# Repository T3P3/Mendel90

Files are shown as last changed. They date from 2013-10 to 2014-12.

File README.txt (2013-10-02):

Mendel90 Lasercut
-----------------
The Think3dPrint3d variation of the Mendel90. Original Mendel90 source available here:
https://github.com/nophead/Mendel90

For the initial announcement of this design see my blog post here:
http://blog.think3dprint3d.com/2013/09/mendel90-laser-cut-ready-to-print.html

IMPORTANT NOTE:
The make_machine.py script will not work properly with this branch of the Mendel90,
the individual scad files will need to be compiled if you change variables. Also note that
the changes are not fully parametric so check the output before printing/lasercutting

======================================================================
Original text of Nophead's readme follows:
======================================================================

Limitations
-----------
Currently only supports mendel and sturdy machine variants, the huxley version needs more work.

Use
---
Add the directory of the OpenScad executable to your search path. For Windows OpenSCAD-2012.02 or later is required. For Linux it will need to be openscad-2011.12 or later.
To get PDF versions of the sheet drawings add InkScape to your search path.

To make all the files for a machine run
    make_machine.py machine_name

To make just the bom, sheets or stls run bom.py, sheets.py or stls.py machine_name.

machine_name can be mendel or sturdy. To make your own variant copy scad\conf\mendel_config.scad or scad\conf\sturdy_config.scad to yourname_config.scad.  Then run make_machine yourname.

To view the model of the whole machine, open scad\main.scad. It will take several minutes to render (about about 8 minutes on my computer) but after that you can pan and zoom it at reasonable speed and changes takes less time to render.  (Note: main.scad will only render correctly if conf\machine.scad exists, which is created by the make_machine.py script.)

To view a sub-assembly, open the individual scad files. Set the exploded flag in config.scad to make exploded views.

To get blender renders of all the parts put blender in your search path and run render.py machine_name.

Credits
-------
Fan model based on http://www.thingiverse.com/thing:8063 by MiseryBot, CC license.

Sanguinololu model http://www.thingiverse.com/thing:18606 by ax_the_b, CC license.

Spring taken from openscad example 20

x-end.scad and wade.scad use some elements of the Prusa ones by Josef Prusa, GPL license.

z_couplings originally based on http://www.thingiverse.com/thing:7153 by Griffin_Nicoll, GPL license.

Bearing holders originally based on http://www.thingiverse.com/thing:7755 by Jolijar, CC license.

InkCL.py based on code from http://kaioa.com/node/42

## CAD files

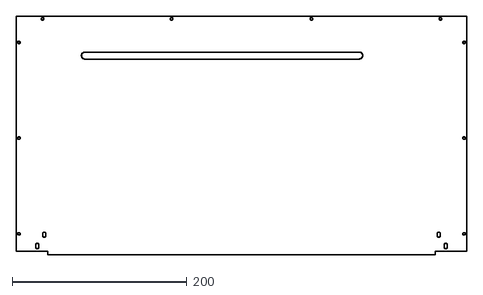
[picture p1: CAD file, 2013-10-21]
lasercut/sheets/T3P3_LC_M90_Acrylic_v1.0_top.dxf
515.5 x 273.0

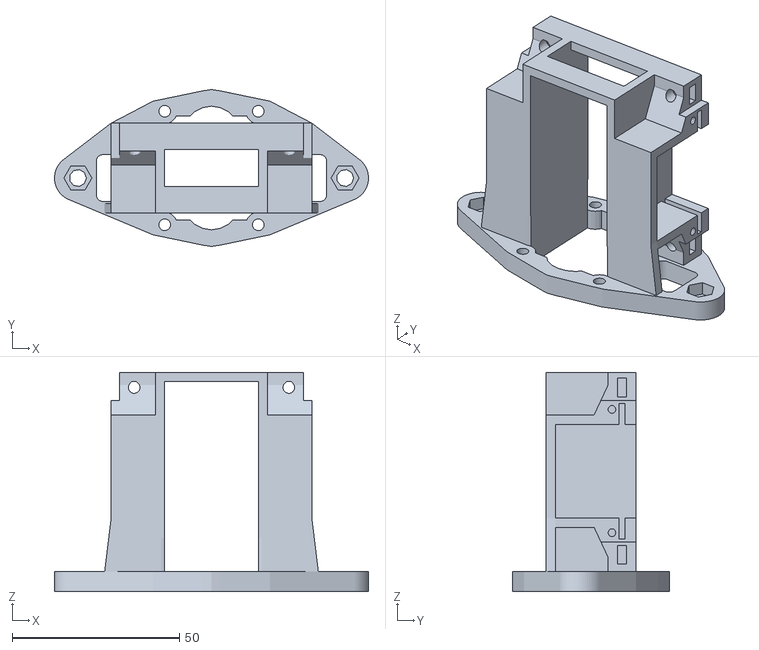
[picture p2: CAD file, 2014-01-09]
lasercut/stls/D_bracket_k_v0.2.stl
94.0 x 47.0 x 65.6

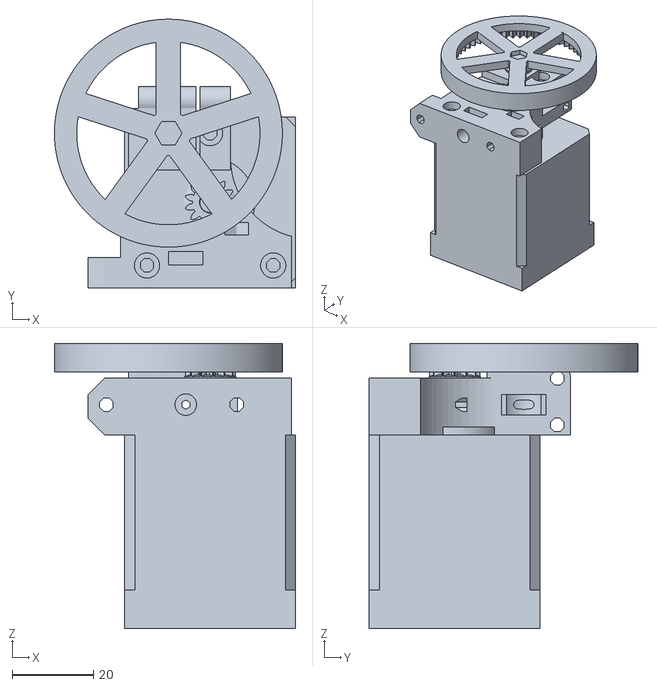
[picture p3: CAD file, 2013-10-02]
scad/rrp_extruder/extruder-drive.stl
59.2 x 66.0 x 70.0

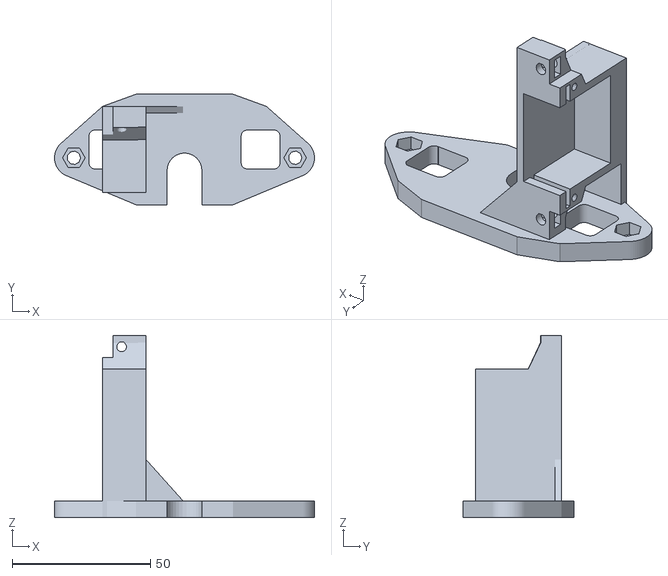
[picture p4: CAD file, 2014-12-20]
V2_upgrades/D_bracket_g_v0.2.stl
94.0 x 40.0 x 65.8

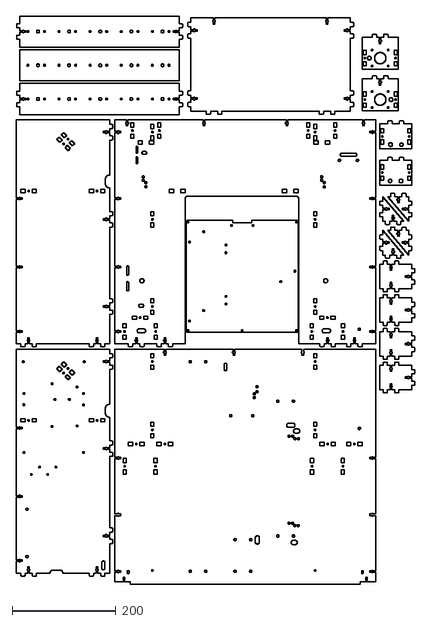
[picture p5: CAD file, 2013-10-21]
lasercut/sheets/T3P3_LC_M90_v1.0.dxf
768.5 x 1095.0

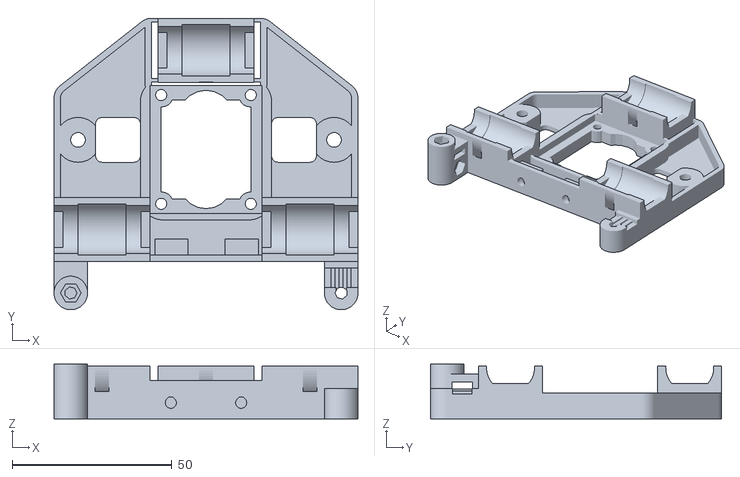
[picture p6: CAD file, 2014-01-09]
lasercut/stls/x-carriage_K_v0.2.stl
95.0 x 91.1 x 17.1

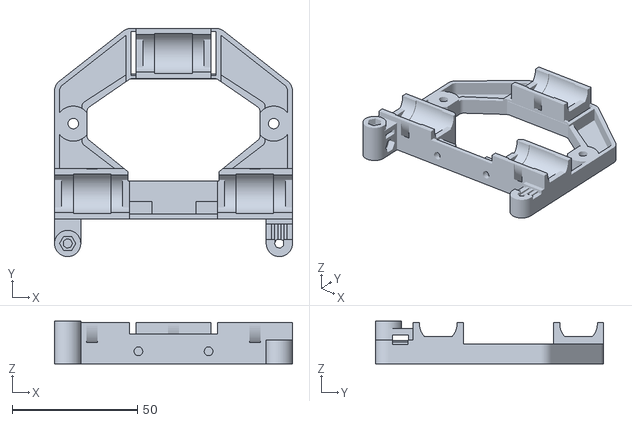
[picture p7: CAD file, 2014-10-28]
V2_upgrades/x-carriage - gv0.3.stl
95.0 x 91.1 x 17.1

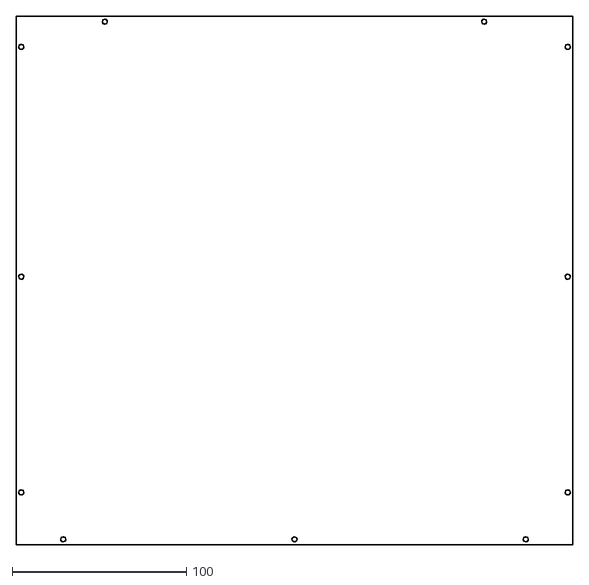
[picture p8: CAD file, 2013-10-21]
lasercut/sheets/T3P3_LC_M90_Acrylic_v1.0_back.dxf
319.9 x 303.6

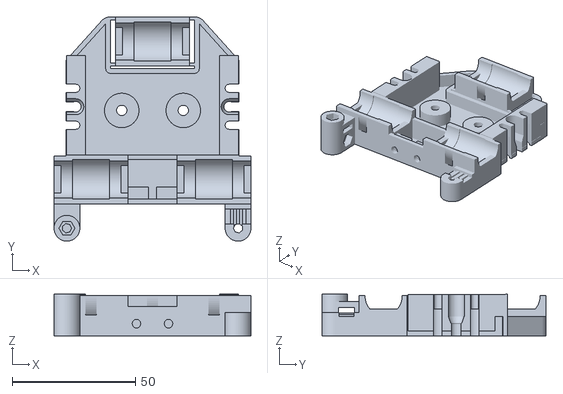
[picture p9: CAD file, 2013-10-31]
lasercut/stls/x-carriage_RRPEv0.3.stl
80.0 x 91.1 x 17.0

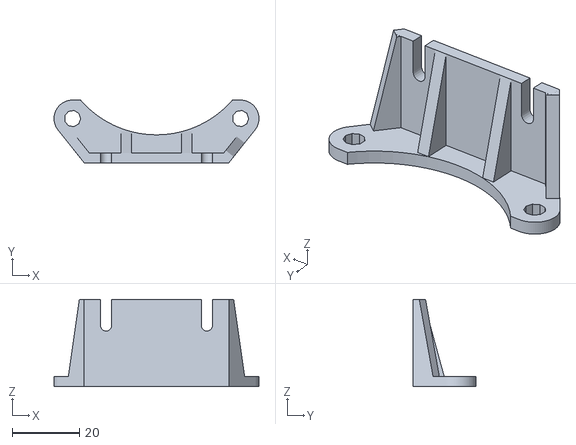
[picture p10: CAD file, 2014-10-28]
V2_upgrades/x_carriage_fan_bracket_e3dv6.stl
61.0 x 18.7 x 26.0

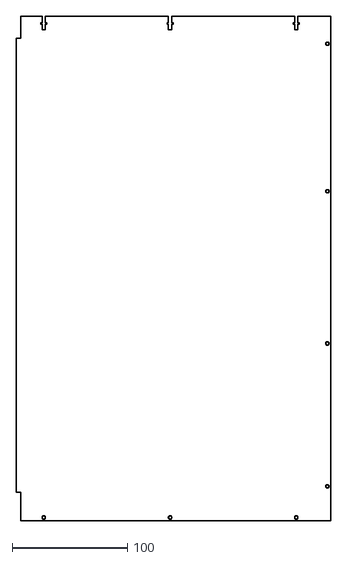
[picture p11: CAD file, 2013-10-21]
lasercut/sheets/T3P3_LC_M90_Acrylic_v1.0_side.dxf
273.0 x 438.0

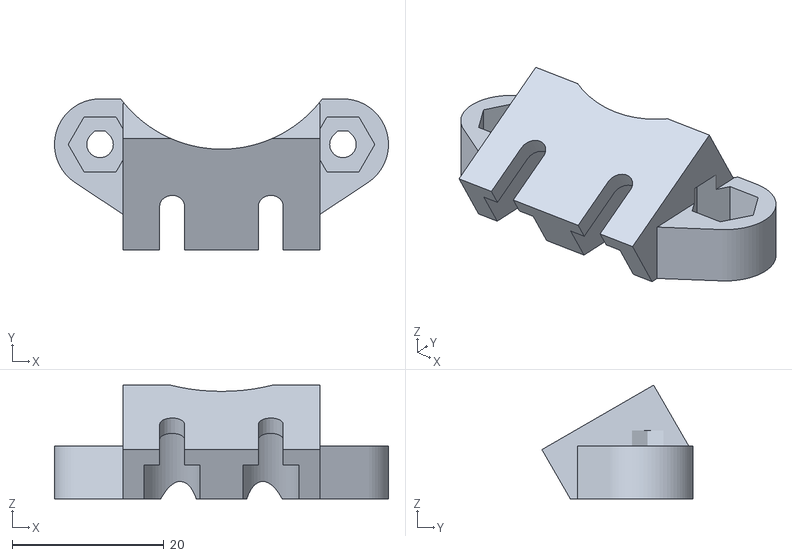
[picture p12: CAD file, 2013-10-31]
lasercut/stls/simple40mmfanbracket_RRPEv0.3.stl
44.0 x 19.9 x 15.0

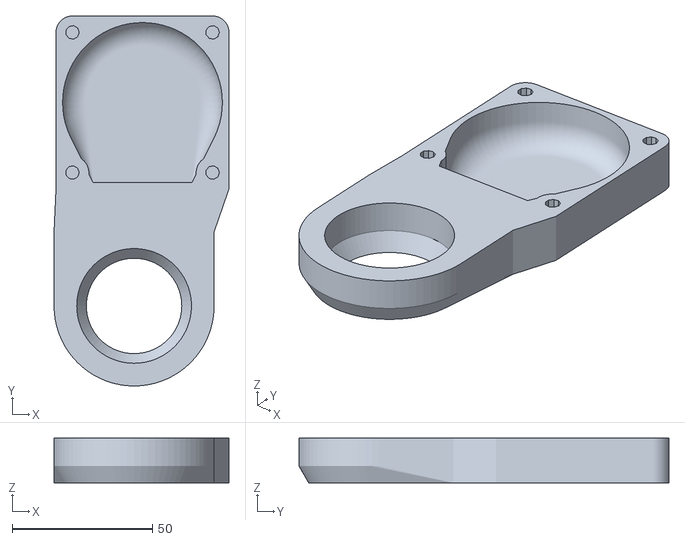
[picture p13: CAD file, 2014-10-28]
V2_upgrades/x_carriage_fan_duct_e3dv6_v2.stl
62.4 x 132.0 x 16.0

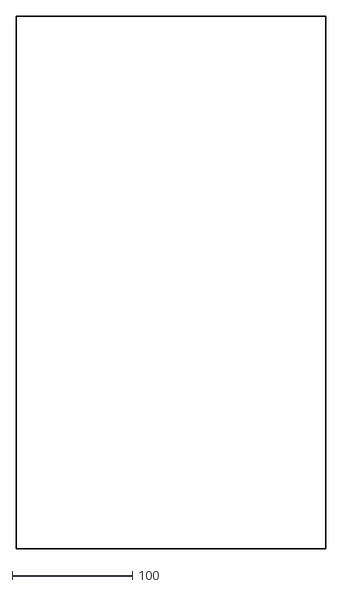
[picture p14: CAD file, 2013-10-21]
lasercut/sheets/T3P3_LC_M90_Acrylic_v1.0_door.dxf
257.8 x 444.0

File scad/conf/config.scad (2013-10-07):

//
// Mendel90
//
// GNU GPL v2
// nop.head@gmail.com
// hydraraptor.blogspot.com
//
// Configuration file
//
bom = $bom == undef ? 0: $bom;                 // 0 no bom, 1 assemblies and stls, 2 vitamins as well
exploded = $exploded == undef ? 0 : $exploded; // 1 for exploded view
//exploded =1;
show_jigs = true;               // show printed jigs required to build the machine
show_support = true;            // show support structures, must be set when generating STLs

// Real-world colors for various parts & vitamins
use_realistic_colors = false;    // true for "real" colors, false for "distinct" colors (useful during design and for build instructions)
printed_plastic_color = "blue";
cable_strip_real_color = "fuchsia";
belt_real_color = "yellow";
bulldog_real_color ="black";

eta = 0.01;                     // small fudge factor to stop CSG barfing on coincident faces.
$fa = 5;
$fs = 0.5;

//
// Hole sizes
//
No2_pilot_radius = 1.7 / 2;       // self tapper into ABS
No4_pilot_radius = 2.0 / 2;       // wood screw into soft wood
No6_pilot_radius = 2.0 / 2;       // wood screw into soft wood

No2_clearance_radius = 2.5 / 2;
No4_clearance_radius = 3.5 / 2;
No6_clearance_radius = 4.0 / 2;

M2p5_tap_radius = 2.05 / 2;
M2p5_clearance_radius= 2.8 / 2;   // M2.5
M2p5_nut_trap_depth = 2.5;

M3_tap_radius = 2.5 / 2;
M3_clearance_radius = 3.3 / 2;
M3_nut_radius = 6.5 / 2;
M3_nut_trap_depth = 3;

M4_tap_radius = 3.3 / 2;
M4_clearance_radius = 2.2;
M4_nut_radius = 8.2 / 2;
M4_nut_trap_depth = 4;

M5_tap_radius = 4.2 / 2;
M5_clearance_radius = 5.3 / 2;
M5_nut_radius = 9.2 / 2;
M5_nut_depth = 4;

M6_tap_radius = 5 / 2;
M6_clearance_radius = 6.4 / 2;
M6_nut_radius = 11.6 / 2;
M6_nut_depth = 5;

M8_tap_radius = 6.75 / 2;
M8_clearance_radius = 8.4 / 2;
M8_nut_radius = 15.4 / 2;
M8_nut_depth = 6.5;

cnc_tool_dia = 0.5;
layer_height = 0.4;
filament_width = layer_height * 1.5;
min_wall = 2 * filament_width + eta;
part_base_thickness = 5;;           // The thickness of things screwed to the frame

pcb_thickness = 1.6;
feed_tube_rad = 5 / 2;              // Filament feed tube
feed_tube_tape_rad = 6.2 / 2;
feed_tube_tape = 12;
nozzle_length = 54;                 // how far nozzle is below top of carriage


include <colors.scad>
include <utils.scad>
include <vitamins.scad>

endstop_wires    = [2, 1.4, "A"];   // 7 strands of 0.2
motor_wires      = [4, 1.4, "B"];
bed_wires        = [2, 2.8, "C"];   // 13A mains cable
fan_motor_wires  = [6, 1.4, "D"];   // fan and motor wires along top of gantry
two_motor_wires  = [8, 1.4,,"E"];   // Y and Z motors
thermistor_wires = endstop_wires;

endstop_wires_hole_radius = wire_hole_radius(endstop_wires);
motor_wires_hole_radius = wire_hole_radius(motor_wires);
two_motor_wires_hole_radius = wire_hole_radius(two_motor_wires);
fan_motor_wires_hole_radius = wire_hole_radius(fan_motor_wires);
bed_wires_hole_radius = wire_hole_radius(bed_wires);
thermistor_wires_hole_radius = wire_hole_radius(thermistor_wires);

cnc_sheets = false;                 // If sheets are cut by CNC we can use slots, etc instead of just round holes
base_nuts = true;                  // Need something under the base if using nuts
pulley_type = T5x8_plastic_pulley;
clip_handles = true;
include_fan = false;
part_fan = fan60x15;
include <machine.scad>              // this file is generated from the command line parameter to include one of the machine configs

screw_clearance_radius = screw_clearance_radius(cap_screw);
nut = screw_nut(cap_screw);
nut_radius = nut_radius(nut);
nut_trap_depth = nut_trap_depth(nut);
washer = screw_washer(cap_screw);

bearing_clamp_tab = cnc_sheets ? (nut_radius(nut) + 3 * filament_width) * 2 : washer_diameter(washer) + 2;   // how much the lugs stick out and their width
bearing_clamp_tab_height = 4;           // thickness of the lugs

hole_edge_clearance = 5;                // how close a hole can be to the edge of a sheet
base_clearance = cnc_sheets ? 4 : 4;    // how close we get to the edge of the base
axis_end_clearance = cnc_sheets ? 4 : 4;// how close we get to the end of an axis
limit_switch_offset = 1;                // the over travel to reach the limit switch
X_carriage_clearance = 2;               // how close the X carriage is to the XZ plane
                                        // how close the Y carriage is to the window in the XZ plane
Y_carriage_clearance = 2 + bulldog_handle_length(small_bulldog) - (Y_carriage_width - bed_width) / 2;
Z_clearance = 10;                       // How close the top of the object gets to the gantry
belt_clearance = 0.2;                   // clearance of belt clamp slots

X_bar_dia = X_bearings[2];      // rod sizes to match the bearings
Y_bar_dia = Y_bearings[2];
Z_bar_dia = Z_bearings[2];

Y_idler_bearing = BB624;
X_idler_bearing = BB624;

extruder_ways = 4 + 6 + 2 + 1 + 1;      // motor + heater(x3) + thermistor + probe + fan = 14
x_end_ways = extruder_ways + 4 + 2;     // motor plus limit switch = 20
bed_ways = 24 + 2;                      // twelve each way for the current plus a thermistor

module wire_hole_or_slot(r) {
    if(cnc_sheets)
        rotate([0, 0, 90])
            slot(r = r, h = 100, l = 2 * r);
    else
        translate([0, r + hole_edge_clearance, 0])
            wire_hole(r);
}

function z_bar_offset() = round(NEMA_width(Z_motor)) / 2;

base_screw = sheet_is_soft(base) ? frame_soft_screw : (base_nuts ? frame_thin_screw : frame_thick_screw);
base_nut = base_nuts ? screw_nut(base_screw) : false;
base_nut_traps = base_nuts && cnc_sheets;
base_washer = screw_washer(base_screw);
base_screw_length = base_nuts ? screw_longer_than(
                                    sheet_thickness(base)
                                    + part_base_thickness +
                                    (cnc_sheets ? 1 : 2) * washer_thickness(base_washer)
                                    + nut_thickness(base_nut, true)
                                  )
                              : screw_shorter_than(
                                    sheet_thickness(base)
                                    + part_base_thickness
                                    + 2 * washer_thickness(base_washer)
                                 );


frame_screw = sheet_is_soft(frame) ? frame_soft_screw : (frame_nuts ? frame_thin_screw : frame_thick_screw);
frame_nut = frame_nuts ? screw_nut(frame_screw) : false;
frame_nut_traps = frame_nuts && cnc_sheets;
frame_washer = screw_washer(frame_screw);
frame_screw_length = frame_nuts ? screw_longer_than(
                                      sheet_thickness(frame)
                                      + part_base_thickness +
                                      (cnc_sheets ? 1 : 2) * washer_thickness(frame_washer)
                                      + nut_thickness(frame_nut, true)
                                  )

                                : screw_shorter_than(
                                      sheet_thickness(frame)
                                      + part_base_thickness
                                      + 2 * washer_thickness(frame_washer)
                                  );

echo("base screw length", base_screw_length);
echo("frame screw length",frame_screw_length);



module frame_screw(thickness) {
    if(frame_nuts && cnc_sheets) {
        nut(frame_nut, true);
        translate([0, 0, -sheet_thickness(frame) - thickness])
            rotate([180, 0, 0])
                screw_and_washer(frame_screw, frame_screw_length);
    }
    else {
        screw_and_washer(frame_screw, frame_screw_length, !frame_nuts);
        if(frame_nuts)
            translate([0, 0, -sheet_thickness(frame) - thickness])
                rotate([180, 0, 0])
                    nut_and_washer(frame_nut, true);
    }
}

module frame_screw_hole() {
    cylinder(r = frame_nuts ? screw_clearance_radius(frame_screw) : screw_pilot_hole(frame_screw), h = 100, center = true);
}



module base_screw(thickness) {
    if(base_nuts && cnc_sheets) {
        nut(base_nut, true);
        translate([0, 0, -sheet_thickness(base) - thickness])
            rotate([180, 0, 0])
                screw_and_washer(base_screw, base_screw_length);
    }
    else {
        screw_and_washer(base_screw, base_screw_length, !base_nuts);
        if(base_nuts)
            translate([0, 0, -sheet_thickness(base) - thickness])
                rotate([180, 0, 0])
                    nut_and_washer(base_nut, true);
    }
}

module base_screw_hole() {
    cylinder(r = base_nuts ? screw_clearance_radius(base_screw) : screw_pilot_hole(base_screw), h = 100, center = true);
}

bar_clamp_depth = 4 + washer_diameter(base_washer);           // how thick the bar clamps are
bar_clamp_tab = 3 + washer_diameter(base_washer);             // how much the lugs stick out
bar_clamp_band = 3;                                           // the thickness of the strap that clamps the bar.

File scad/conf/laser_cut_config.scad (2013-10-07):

//
// Mendel90
//
// GNU GPL v2
// nop.head@gmail.com
// hydraraptor.blogspot.com
//
// Configuration file
//

echo("LaserCut:");

Z_bearings = LM8UU;
Y_bearings = LM8UU;
X_bearings = LM8UU;

X_motor = NEMA17;
Y_motor = NEMA17;
Z_motor = NEMA17;

hot_end = JHeadMk5;

X_travel = 200;
Y_travel = 200;
Z_travel = 200;

bed_depth = 214;
bed_width = 214;
bed_pillars = M3x20_pillar;
bed_glass = glass2;
bed_thickness = pcb_thickness + sheet_thickness(bed_glass);    // PCB heater plus glass sheet
bed_holes = [209, 209];


base = MelamineMDF6;          
base_corners = 0;
base_nuts = true;

frame = MelamineMDF6;
frame_corners = 0;
frame_nuts = true;

case_fan = fan80x38;
psu = ALPINE500;
controller = RAMPS;
spool = spool_300x85;
bottom_limit_switch = false;
top_limit_switch = true;

single_piece_frame = true;
stays_from_window = false;
cnc_sheets = true;                 // If sheets are cut by CNC we can use slots, etc instead of just round holes
lc_sheets = true; //use the laser cut fixing method and additional slots for ease of assembly
lc_fixing_offset=24; //how far from an edge to put a LC fixing
lc_fixing_screw_type = M3_cap_screw;  
lc_fixing_screw_length = 16; //sheet_thickness(base)+10;

//additional dimensions for some sheets for LC M90
base_w_LC = 468.5+35;//base_width+10+25;
base_d_LC = 425+28;//base_depth+28;
height_LC = 390+12+30;//height+12+53;
stay_depth_LC=166+14;//stay_depth+14;
stay_height_LC=height_LC;


pulley_type = T2p5x16_metal_pulley;

Y_carriage = DiBond;

X_belt = T2p5x6;
Y_belt = T2p5x6;

motor_shaft = 5;
Z_screw_dia = 5;            // Studding for Z axis

Y_carriage_depth = bed_holes[1] + 7;
Y_carriage_width = bed_holes[0] + 7;

Z_nut_radius = M5_nut_radius;
Z_nut_depth = M5_nut_depth;
Z_nut = M5_nut;

//
// Default screw use where size doesn't matter
//
cap_screw = M3_cap_screw;
hex_screw = M3_hex_screw;
//
// Screw for the frame and base
//
frame_soft_screw = No6_screw;               // Used when sheet material is soft, e.g. wood
frame_thin_screw = M4_cap_screw;            // Used with nuts when sheets are thin
frame_thick_screw = M4_pan_screw;           // Used with tapped holes when sheets are thick and hard, e.g. plastic or metal
//
// Feature sizes
//
default_wall = 3;
thick_wall = 4;

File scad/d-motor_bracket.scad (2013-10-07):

//
// Mendel90
//
// GNU GPL v2
// nop.head@gmail.com
// hydraraptor.blogspot.com
//
// Bracket to mount 9 way D type to back of motor
//
include <conf/config.scad>
use <ribbon_clamp.scad>

connector = DCONN15;
pcb = true;
idc = true;

thickness = 2.4;
lid_thickness = 2.4;

wall = 2;
front_thickness = wall + No2_pilot_radius + washer_diameter(M2p5_washer) / 2 + 1;
slot_width = d_slot_length(connector);
slot_height = 11;
face_height = 13;
flange_clearance = 0.7;
flange_width = d_flange_length(connector) + 2 * flange_clearance;
flange_height = d_flange_width(connector) + flange_clearance;
flange_thickness = d_flange_thickness(connector) + flange_clearance;


overlap = 5;                            // how much it overlaps the side of the motor
//length = overlap + thickness + (pcb ? 14 : 20);
length = overlap + thickness + 20;
height = slot_height / 2 + face_height / 2 + thickness;
d_width = flange_width + 2 * wall;
nut_slot = nut_thickness(M3_nut) + 0.3;
lug_depth = nut_slot + 3 * wall;
lug_width = 2 * nut_flat_radius(M3_nut) + wall;
lug_height = thickness + slot_height / 2 + M3_nut_radius;
screw_x = length - wall - No2_pilot_radius;
screw_y = (d_width + slot_width) / 4;
pitch = d_width + 2 * nut_flat_radius(M3_nut);

cable_guide_width = 20;
cable_guide_thickness = 4;
cable_screw = M3_cap_screw;

shell_front = front_thickness;
shell_length = shell_front + 12 + ribbon_clamp_width(cable_screw);
shell_screw_x = shell_length - wall - No2_pilot_radius;

pcb_width = 24.13;
pcb_length = 33.02;
pcb_offset = 3 * 1.27;


nut_x = length + flange_thickness + wall -lug_depth + wall;

function d_motor_bracket_offset(motor) = NEMA_holes(motor)[0] + screw_head_radius(M3_cap_screw) + d_width / 2 + lug_width;

//
// Lid to retain connector and nuts
//
module d_motor_bracket_lid_stl(motor = NEMA17, nuts = true) {
    if(nuts)
        stl("d_motor_bracket_lid");
    else
        stl("d_shell_lid");

    lid_width = front_thickness + flange_thickness + wall;
    nut_cover_width = d_width + 2 * lug_width;
    nut_cover_height = height + lid_thickness - lug_height - flange_clearance;
    nut_cover_depth = lug_depth;

    difference() {
        union() {
            if(nuts) {
                translate([length - front_thickness + lid_width - nut_cover_depth / 2, 0, 0])
                    rounded_rectangle([nut_cover_depth, nut_cover_width, nut_cover_height], 2, center = false);
                for(side = [-1, 1])
                    translate([screw_x,  side * screw_y, 0])
                        cylinder(r = washer_diameter(M2p5_washer) / 2 + 2, h = lid_thickness);
            }
            else
                translate([length - front_thickness + lid_width / 2, 0, 0])
                    rounded_rectangle([lid_width, d_width, lid_thickness], 2, center = false);
        }

        if(nuts)
            translate([length - nut_cover_depth, -d_width / 2 - flange_clearance, lid_thickness - eta])
                cube([nut_cover_depth * 2, d_width + 2 * flange_clearance, 10]);

        for(side = [-1, 1])
            translate([screw_x,  side * screw_y, 0])
                rotate([0, 0, -side * 360 / 20])
                    poly_cylinder(r = No2_clearance_radius, h = 100, center = true);
    }
}

module d_shell_lid_stl() d_motor_bracket_lid_stl(motor = NEMA17, nuts = false);
//
// Attaches to the motor
//
module d_motor_bracket_stl(motor = NEMA17) {
    stl("d_motor_bracket");

    m_width = NEMA_width(motor) + 2 * thickness;
    offset = d_motor_bracket_offset(motor) + (m_width - d_width) / 2;
    mouth = pitch + 2 * M3_clearance_radius + layer_height / 2;

    difference() {
        union() {
            linear_extrude(height = thickness, convexity = 5)       // base
                polygon(points = [ [0,                        0],
                                   [overlap,                  0],
                                   [overlap,             offset],
                                   [length - eta,        offset],
                                   [length - eta,        offset + d_width],
                                   [overlap,             offset + d_width],
                                   [overlap,             m_width],
                                   [0,                   m_width],
                                 ]);

            translate([overlap , 0, eta])                               // motor wall
                cube([thickness, d_width + offset, height]);

            for(y = [0, m_width - thickness])                           // buttresses
                translate([overlap + eta, y, thickness - eta])
                    rotate([90, 0, 180])
                        right_triangle(width = overlap, height = height - thickness, h = thickness, center = false);


            difference() {
                union() {
                    // connector wall
                    translate([length - front_thickness, offset, eta])
                        cube([front_thickness + flange_thickness + wall, d_width, height]);

                    // nut lugs
                    translate([length + flange_thickness + wall - lug_depth / 2, offset + d_width / 2, eta])
                        rounded_rectangle([lug_depth, d_width + 2 * lug_width, lug_height], r = 2, center = false);

                    // d side walls
                    for(y = [0, d_width - thickness])
                        translate([overlap, y + offset, eta])
                            cube([length - overlap, thickness, height]);
                }

                translate([length, offset + (d_width - flange_width) / 2, thickness + slot_height / 2 - flange_height / 2])
                    cube([flange_thickness, flange_width, 20]);                         // slot for flange

                translate([10, d_width / 2 - slot_width / 2 + offset, thickness + eta * 2])  //slot for connector body
                    cube([30, slot_width, 20]);


                for(side = [-1, 1]) {
                    translate([nut_x + nut_slot / 2, d_width / 2 - side * pitch / 2 + offset, thickness + slot_height / 2]) //connector screws
                        rotate([90, 0, 90]) {
                            rotate([0,0,30])
                                nut_trap(1, M3_nut_radius, nut_slot / 2, true);

                            translate([0, 5, 0])
                                cube([nut_flat_radius(M3_nut) * 2, 10, nut_slot], center = true);

                            teardrop_plus(r = M3_clearance_radius, h = 100, center = true);
                        }

                    translate([screw_x, d_width / 2 - side * screw_y + offset, height + lid_thickness])         // lid screws holes
                        rotate([0,0,180])
                            poly_cylinder(r = No2_pilot_radius, h = 12 * 2, center = true);
                }

            }


        }
        for(y = NEMA_holes(motor))                                                          // motor screws
            for(z = NEMA_holes(motor))
                translate([overlap - 1, m_width / 2 + y, NEMA_width(motor) / 2 + thickness + z])
                    rotate([90,0,90])
                        teardrop_plus(r = M3_clearance_radius, h = thickness + 2, center = false);
    }
}
//
// Attaches connector to ribbon cable and plastic strip
//
function d_motor_connector_offset(motor) = [
    NEMA_width(motor) / 2 + thickness - cable_guide_thickness + ribbon_clamp_slot_depth(),
    -NEMA_length(motor) + overlap - length - d_mate_distance(connector) - shell_length + ribbon_clamp_width(cable_screw),
    d_motor_bracket_offset(motor)
];

module d_shell_stl() {
    stl("d_shell");

    mouth = pitch + 2 * screw_clearance_radius(cable_screw) + layer_height / 2;
    rad = ribbon_clamp_width(cable_screw) / 2;
    clamp_pitch = ribbon_clamp_pitch(extruder_ways, cable_screw);

    front = shell_front + flange_thickness + wall;
    union() {
        difference() {
            union() {
               // screw lugs
               translate([shell_length + flange_thickness + wall - front / 2, d_width / 2, eta])
                    rounded_rectangle([front, d_width + 2 * lug_width,
                                       thickness + slot_height / 2 + washer_diameter(M3_washer) / 2 + 1], r = 2, center = false);

               translate([shell_length + flange_thickness + wall - front / 2, d_width / 2, eta])        // connector wall
                    rounded_rectangle([front, d_width, height], r = 2, center = false);

               linear_extrude(height = cable_guide_thickness, convexity = 5)
                    hull() {
                        for(side = [-1,1])
                            translate([rad, d_width / 2 + side * clamp_pitch / 2])
                                circle(r = rad, center = true);

                        translate([shell_length - shell_front, 0])
                            square([1, d_width]);
                    }
            }
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

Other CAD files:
lasercut/stls/D_bracket_RRPEv0.3.stl
lasercut/stls/x_end_clamp.stl
lasercut/stls/x_carriage_fan_duct.stl
lasercut/stls/x_motor_ribbon_bracket.stl
scad/z-motor-bracket.scad
V2_upgrades/x-carriage - gv1.scad
lasercut/stls/ATX_PSU_brackets.stl
lasercut/stls/alu_channel_cap.stl
lasercut/stls/d-motor_bracket.stl
lasercut/stls/d_motor_bracket.stl
lasercut/stls/d_motor_bracket_lid.stl
lasercut/stls/d_shell.stl
lasercut/stls/d_shell_lid.stl
lasercut/stls/ribbon_clamp_14_33.stl
lasercut/stls/ribbon_clamp_14_33NB.stl
lasercut/stls/ribbon_clamp_20_33.stl
lasercut/stls/ribbon_clamp_20_44.stl
lasercut/stls/ribbon_clamp_20_44N.stl
lasercut/stls/ribbon_clamp_26_33.stl
lasercut/stls/ribbon_clamp_26_33N.stl
lasercut/stls/ribbon_clamp_26_44N.stl
lasercut/stls/ribbon_clamps.stl
lasercut/stls/wades_big_gear.stl
lasercut/stls/wades_block.stl
lasercut/stls/wades_gear_spacer.stl
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

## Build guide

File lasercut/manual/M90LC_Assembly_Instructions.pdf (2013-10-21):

www.think3dprint3d.com

# Mendel90 Laser Cut Kit Assembly Instructions

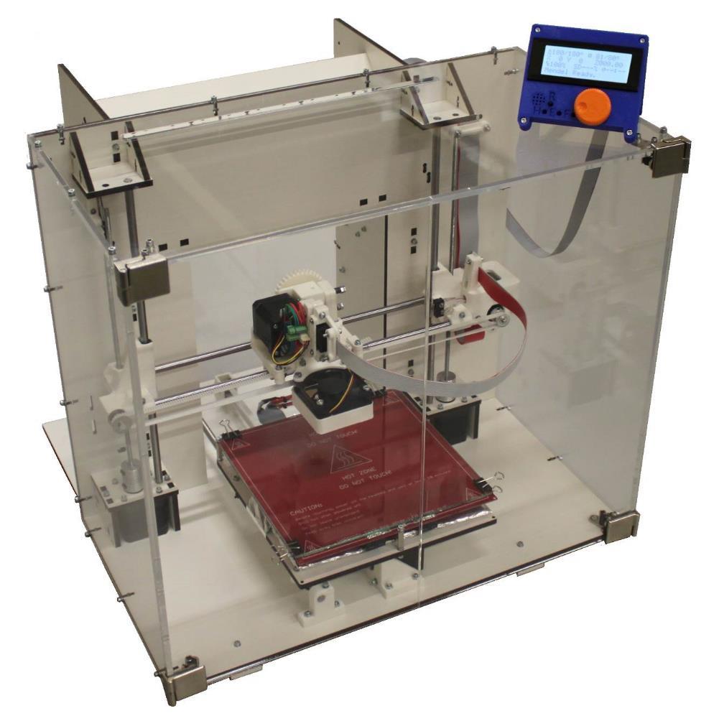
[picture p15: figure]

M90LC Manual | 2 of 70 | V0.4-20131016

### 1. Acknowledgements

The Mendel 90 Lasercut design is based on the Mendel90 design (http://hydraraptor.blogspot.co.uk/2012/12/mendel90-updates.html) by Chris Palmer (Nophead) and this build manual uses some of the original Mendel90 build manual where the assembly process is similar.

### 2. License

This manual and the source code for the Mendel 90 LC (https://github.com/T3P3/Mendel90) are both licensed under the GPL v2.0. It is based on work by Nophead which is licensed under the GPL v2.0.

### 3. Changes

19/10/13 – Integrating initial customer feedback 08/10/13 – Final review prior to first publication. 07/10/13 – Added acrylic enclosure section. 06/10/13 – New X end design pictures added. 03/10/13 – Beta tester feedback integrated. 27/09/13 – Initial version.

M90LC Manual | 3 of 70 | V0.4-20131016

### 4. Table of Contents

M90LC Manual | 4 of 70 | V0.4-20131016

M90LC Manual | 5 of 70 | V0.4-20131016

### 5. Kit Contents

The kit contains the following items, Detailed lists (Bills of Material/BOMs) are included in each subsection of the manual

- Laser cut frame and aluminium base channels
- Printed Parts
- Fasteners
- Bearings
- Rods
- Motors
- Hot end and heated print bed.
- Electronics and wiring, including LCD display
- Power supply
- Starter PLA filament pack (note that it will vary from that pictured above)
- Laser cut acrylic enclosure (optional extra)

M90LC Manual | 6 of 70 | V0.4-20131016

### 6. General Build Tips

- The build is broken down into sub-assemblies that can be worked on sequentially by one person, or in parallel if there is more than one person building.
- To make it easier to find the relevant section, the sub-assembly sections are in the order X, Y, Z, and E. This does not mean they have to be tackled in this order.
- Once the sub-assemblies are completed, the suggested assembly order is Frame, Y-axis, Z-axis, X-axis and Electronics
- Looking at the printer from the front, X is left / right. Y is backwards / forwards. Z is up / down. The origin X=0, Y=0, Z=0 is at the front left-hand corner of the print bed glass, touching the glass
- Bar lengths: The longest and shortest bars are the Y bars. Of the two pairs left, the longer ones are the X axis and the shorter ones the Z axis.
- The longer belt is for X and the shorter one is for Y.
- De-grease the rods that come with packing grease. (You will need to lubricate them again after assembly).
- All screws have a plain washer where they meet the plastic, to spread the load and prevent the plastic being chewed up by the rotation of the screw head. Most plastic parts have a captive nyloc nut to prevent them vibrating loose. We supply our kits with all captive nuts already inserted to speed up assembly. In case any of them should fall out, plastic parts are supplied bagged. You should carefully check the bag for any loose nuts and add them to the loose nuts supplied, ready for when they are needed.
- You may have some washers, nuts and smaller screws left over at the end of the assembly. This is because we provide spares of the small easy-to-lose items.
- The bar clamps should not be over tightened, i.e. do not close the gap fully or the parts could break. The Y and Z bars only need a light clamping force because the only force trying to slide them is the bearing friction. Washers tend to have a smooth side and a side with a burr from being stamped out. Make sure the smooth side faces bearings and belts.
- The laser-cutting process does not produce perfectly square 90° cuts because the cutting beam is focussed to a point and so makes a tapered cut. This means that some parts will have a “right” side and a “wrong” side. This is particularly true of the Z-motor brackets where the projecting 22mm diameter boss or spigot of the motor should only fit easily from one side of the top plates. The square nuts used for assembly of the MDF frame and acrylic cabinet will also fit into their slots (and fall out of them) much more easily from one side that the other.
- Zip-ties (cable ties) are used for securing cables and also linear bearings. Only those used for linear bearings are listed in the Bill of Materials (BOM) for each section, but we supply enough for all cable management and a few spares as well.
- Ribbon clamp notation is <number of wires>_<hole size>. There are three lengths: the short ones are 14 way for the X axis, the medium ones are 20 way for the Z axis and the long ones are 26 way for the bed. An N suffix denotes with nut traps. B denotes no slot.

M90LC Manual | 7 of 70 | V0.4-20131016

M90LC Manual | 8 of 70 | V0.4-20131016

### 7. Tools

Required

- Spanners: 5.5mm (¼ drive socket supplied), 7mm & 13mm.
- Allen keys: 1.5mm, 2mm, 2.5mm, 3mm - Supplied
- PZ 1 Pozi-drive screw driver.
- Digital callipers

Recommended

- Multi-meter with thermocouple attachment
- Dial gauge
- Wire brush
- Consumables
- Lithium/PTFE grease, glass cleaner (acetone recommended), lint free wipes.

M90LC Manual | 9 of 70 | V0.4-20131016

### 8. X-Axis Sub-Assemblies

X-idler

BOM

Category | Description | Qty | Comments
Mechanical | Bearing, ball, 624-ZZ | 2
Mechanical | Bearing, linear, LM8UU | 2 | Pre-fitted
Printed | X idler bracket | 1
Printed | X_end_clamp | 2
Fasteners | M3x20 socket cap screw | 8
Fasteners | M3 form A flat washer | 8
Fasteners | M3 nyloc nut | 8 | Pre-fitted
Fasteners | M4x45 socket cap screw | 1
Fasteners | M4 form A flat washer | 2
Fasteners | M4 x 20 x 1.25 Penny washer | 2
Fasteners | M4 nyloc nut | 1 | Pre-fitted
Fasteners | M5 brass full nut | 1 | Pre-fitted

Method

1. Fit the end clamps to the idler bracket, rounded corners facing outwards, using the M3 x 20 socket cap screws with flat washers between the screw head and the plastic. Ensure the screws engage in the nylon inserts in the pre-fitted nyloc nuts but do not tighten them fully.
1. Make the washer and bearing kebab on the long M4 bolt that forms the idler axle, but leave it loose to allow the X bars to be inserted later.

2.

M90LC Manual | 10 of 70 | V0.4-20131016

X-motor

BOM

Category | Description | Qty | Comments
Electrical | Extruder/X-motor wiring loom | 1
Electrical | Micro switch end stops | 1
Mechanical | Bearing, linear, LM8UU | 2 | Pre-fitted
Mechanical | Timing pulley T2.5-16T, M4 grub screw | 1
Mechanical | Stepper motor NEMA17 high-torque 44Ncm | 1
Sundries | Polypropylene strip 270 x 33 x 0.5 | 1
Sundries | Polypropylene strip 400 x 18 x 0.5 | 1
Printed | d_shell | 1
Printed | d_shell_lid | 1
Printed | ribbon_clamp_14_33 | 1
Printed | ribbon_clamp_14_33NB | 1
Printed | ribbon_clamp_20_33 | 1
Printed | x_motor_bracket | 1
Printed | x_motor_ribbon_bracket | 1 | Pre-fitted
Printed | X_end_clamp | 2
Fasteners | M3x10 socket cap screw | 2
Fasteners | M3x16 socket cap screw | 6
Fasteners | M3x20 socket cap screw | 10
Fasteners | M3x45 socket cap screw | 2 | Pre-fitted
Fasteners | M3 form A flat washer | 19 | 17?
Fasteners | M3 external shake proof washer | 3 | 2?
Fasteners | M3 nyloc nut | 14 | Pre-fitted
Fasteners | No 2 x 1/2 Pozi pan S/T screw | 4
Fasteners | M2.5 flat washer x 5.9 x 0.5 | 4
Fasteners | Nitrile O-ring 2.5 x 1.6 | 2
Fasteners | M5 brass full nut | 1 | Pre-fitted

Illustration

10

M90LC Manual | 11 of 70 | V0.4-20131016

Method

1. Insert the D-connector into the d_shell printed part in the orientation shown below.
2. Secure the connector by screwing on the d_shell_lid with two No2 x 13mm posi pan self-tapping screws with M2.5 washers.
3. Clamp down the cable with the thinnest polypropylene strip under it (against the D shell) using the ribbon_clamp_14_33NB, M3 x 16mm cap screws and M3 washers (from the underside).
4. Complete the D connector by adding M3 x 20mm socket cap screws and flat washers and then secure them in place with the rubber O rings.
5. Fit the pulley to the motor shaft so that 3mm of the shaft protrudes beyond the pulley. Don’t over tighten the grub screw.
6. Fit the motor with the pre-fitted ribbon bracket at the top and secure it to the front of the motor bracket with two M3 x 10 socket cap screws, star washers and plain washers
7. Motors have a ± 1mm tolerance on their length so the bracket at the back may have up to 2mm clearance. We check this and supply extra washers if needed. If there is a gap then

M90LC Manual | 12 of 70 | V0.4-20131016

pack it with M3 washers using between 1 and 5. Screw the M3 x 45mm cap screw through the hole in bracket, the washers (if fitted) and into the motor. The head of the screw will hold the back corner of the motor in the bracket

8.

9. Clamp the 14 way cable and the thinner polypropylene strip in the ribbon clamp on the top of the X motor bracket with the red edge at the top using the ribbon_clamp_14_33, M3 x 16mm socket cap screws and M3 washers. Form the cable and strip into a loop as shown in the picture below before tightening the clamp fully. This is necessary because the cable needs to be a bit longer than the strip to go round the outside of the curve.
10. Clamp the full 20 way part of the cable onto the x_motor_ribbon_bracket at the rear of the motor with the second polypropylene strip on top using the ribbon_clamp_20_33 with M3 x 16mm socket cap screws and M3 washers..
11. It is recommended to add loops of sticky tape (not provided) to fasten the middle of each cable to the middle of its cable strip.
12. Insert the eight M3 x20mm bar clamp socket cap screws as described above for the X idler assembly.

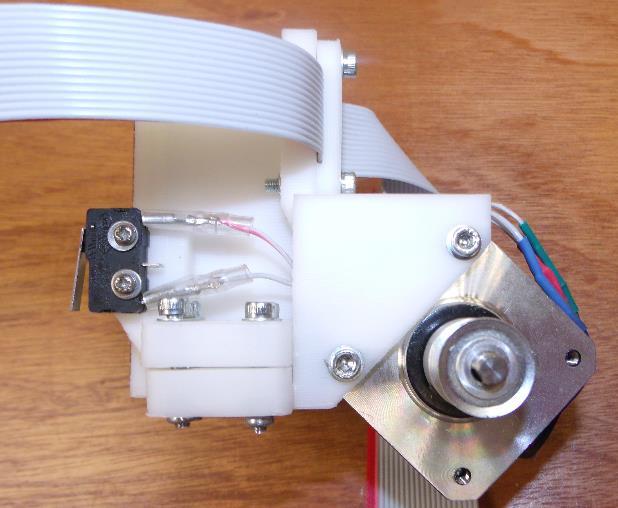
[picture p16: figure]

M90LC Manual | 13 of 70 | V0.4-20131016
13. Pass the two x-endstop wires with spade connectors fitted out through the hole for the limit switch. Plug the spade connectors securely onto the switch using the top and bottom pins (it does not matter which way round they are) and then mount it with two No2 x 13mm pozi pan self-tapping screws with M2.5 washers. N.B. The micro switch must be oriented with the button towards the top. Bend the bottom pin upwards slightly so the spade connector clears the head of the nearest socket cap screw.
14. Pass the X-motor cable down through around the motor and plug it into the connector (make sure the plug is the right way round and do not try to force it).

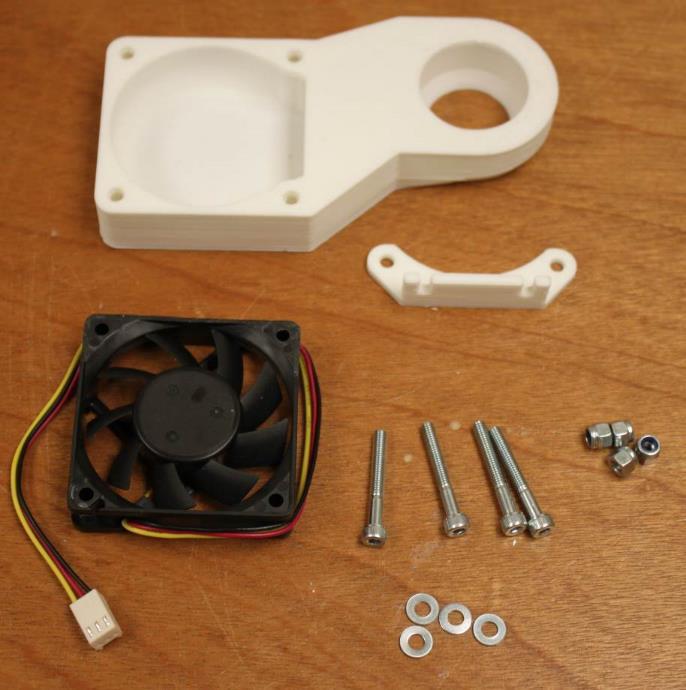
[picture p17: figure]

M90LC Manual | 14 of 70 | V0.4-20131016

### 1.3 X-carriage-fan

BOM

Category | Description | Qty | Comments
Electrical | Extruder fan 60mm x 15mm | 1 | Modified, see below
Printed | x_carriage_fan_bracket | 1
Printed | x-carriage_fan_duct | 1
Fasteners | M4x30 socket cap screw | 4
Fasteners | M4 form A flat washer | 4
Fasteners | M4 nyloc nut | 4 | Pre-fitted

Method

1. The fan is fitted with the label downwards. Examine the top of the fan and identify the edge where the rim has been cut away (opposite side to the cable exit). This is the side on which the fan bracket is mounted.

M90LC Manual | 15 of 70 | V0.4-20131016
2. Assemble as shown below with the fan label downwards and the wires exiting in the front, nearest the leftmost screw in the picture.

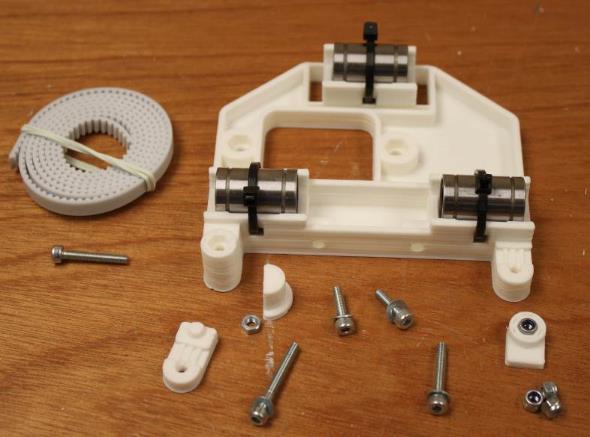
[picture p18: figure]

M90LC Manual | 16 of 70 | V0.4-20131016

### 1.4 X-carriage

BOM

Category | Description | Qty | Comments
Mechanical | Bearing, linear, LM8UU | 3 | Pre-fitted
Mechanical | T2.5 timing belt X=860mm | 1
Sundries | Zip ties 120 long | 3 | Pre-fitted
Printed | x_belt_clamp | 1
Printed | x_belt_grip | 1
Printed | x_belt_tensioner | 1
Printed | x-carriage | 1
Fasteners | M3x12 socket cap screw | 2
Fasteners | M3x20 socket cap screw | 2
Fasteners | M3x25 socket cap screw | 1
Fasteners | M3 form A flat washer | 4
Fasteners | M3 full nut | 1 | Pre-Fitted
Fasteners | M3 nyloc nut | 4 | Pre- Fitted

Method

M90LC Manual | 17 of 70 | V0.4-20131016
1. Insert the two M3 x 12mm screws and washers for the fan mount into the pre-fitted captive nuts but leave loose.
2. Attach the X belt (longer of the two) to the left side x_belt_clamp (RHS in the picture above) with the teeth facing upwards (downwards in the picture) and four complete teeth projecting from the clamp. The teeth slot into the grip grooves in the clamp to help the orientation. Clamp with the M3 x 20mm socket cap screw and washer.
3. Insert a M3 x 20mm socket cap screw for the belt tensioner into the pre-fitted captive nut
3. Holding the X-carriage with the bearings facing up so the two bearings are closest to you. Pull the attached part of belt out to the right, then pass it underneath. Put one half-twist in the belt away from yourself so the teeth also face away (to avoid them catching on the fan) and the flat side is now facing up. Follow the belt around and pass the other end of the belt through the gap above the tensioner (the teeth should be up).
4. Put the tensioning piece on the end of the screw with the flange towards the carriage. Then double back the belt over the tensioner (as depicted in yellow above) and clamp it with the x_belt_grip (with the teeth fitting in the grooves) and an M3 x 25mm cap screw and washer with four complete teeth projecting.

5.

M90LC Manual | 18 of 70 | V0.4-20131016

### 9. Y-Axis Sub-Assemblies

Y-idler

BOM

Category | Description | Qty | Comments
Mechanical | Bearing, ball, 624-ZZ | 2
Printed | y-idler-bracket | 1
Fasteners | M4x20 socket cap screw | 1
Fasteners | M4x30 socket cap screw | 1
Fasteners | M4 form A flat washer | 5
Fasteners | M4 x 20 x 1.25 Penny washer | 2
Fasteners | M4 nyloc nut | 2 | 1 pre-fitted

Method

M90LC Manual | 19 of 70 | V0.4-20131016

Assemble as shown. This is easiest done using a zip tie to assemble the stack in order and then pull it tight to fit the stack into the idler body.

Once in straight the zip tie can be gently replaced with the long M4x30 mm bolt. Do not forget to put M4 washers on the M4 bolt on both sides of the Y-idler.

Screw the M4x 20mm bolt with washer loosely into the captive M4 nut for the time being so it does not get lost.

M90LC Manual | 20 of 70 | V0.4-20131016

Y-motor

BOM

Category | Description | Qty | Comments
Mechanical | Stepper motor NEMA17 high-torque 44Ncm | 1
Mechanical | Timing pulley T2.5-16T, M4 grub screw | 1
Electrical | Y-motor cable - 1.00 long | 1
Printed | y-motor-bracket | 1
Fasteners | M3x10 socket cap screw | 4
Fasteners | M3 form A flat washer | 4
Fasteners | M3 external shake proof (star) washer | 4
Fasteners | M4x20 socket cap screw | 4
Fasteners | M4 form A flat washer | 4
Fasteners | M4 nyloc nut | 4 | fitted

Method

1. Attach the pulley to the motor using the grub screw with about 3mm spare at the end, do not over tighten the grub screw
2. Slide the motor into the gap as above with the plug on the left hand side as viewed facing the shaft. Secure the motor in place using the 4 M3x 10mm screws with star and flat washers, loosely at first then tightening them all evenly.
3. Loosely insert the M4 x 20 socket cap screws and washers into the captive nuts, so they are not misplaced. The Y motor cable will be plugged in later.

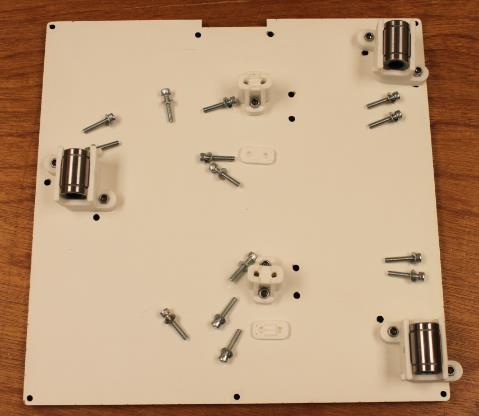
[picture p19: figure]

M90LC Manual | 21 of 70 | V0.4-20131016

Y-carriage

BOM

Category | Description | Qty | Comments
Mechanical | Bearing, linear, LM8UU | 3 | Pre-fitted
MDF | Laser-cut MDF y-carriage | 1
Printed | y_bearing_mount | 1
Printed | y-belt-anchors | 1
Printed | y_belt_anchor_toothed | 1
Printed | y_belt_clip | 1
Printed | y_belt_clip_toothed | 1
Fasteners | M3x16 socket cap screw | 14
Fasteners | M3 form A flat washer | 14
Fasteners | M3 nyloc nut | 14 | Pre-fitted
Sundries | Zip ties 120 long | 3 | Pre-fitted

Method

This view is from the bottom of the bed. The cut out section goes at the back of the machine. The nuts go on the bottom and the screw heads and washers on top. The majority of the holes should

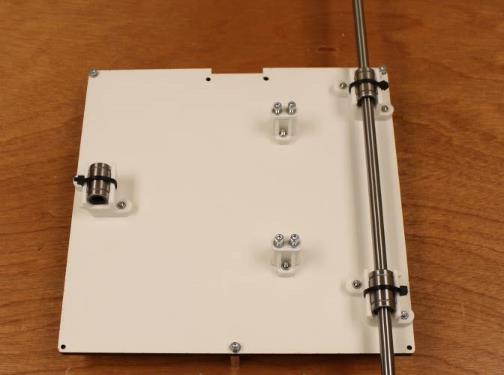
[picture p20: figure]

M90LC Manual | 22 of 70 | V0.4-20131016

be on your right with the cut out section for the ribbon cable furthest from you.

1.

2. Fit the belt clamps loosely to their respective anchors using M3 x 16mm socket cap screws and washers. The clamp with the tooth fits the anchor without teeth and vice versa. Fit the anchors securely to the carriage using M3 x 16mm socket cap screw and washers. Note that the anchor with the tooth is closest to the cut out section, the belt clamp with the tooth at therefore at the front.
3. Bolt the linear bearing holders to the carriage using M3 x 16mm socket cap screws and washers. Note that one side of the bearing holders has a tab to trigger the limit switch, which must face forwards (that is, away from the ribbon clamp slot). Do not completely tighten the M3x16 bolts at this stage, they are tightened after being aligned.
4. Align the two bearings on the left (right on the picture) by gently inserting a rod with a twisting motion (to avoid knocking the balls out of the linear bearing) and lining up the tabs with the edge of the board before tightening the bolts. Leave the third bearing loose.

M90LC Manual | 23 of 70 | V0.4-20131016

Y-heatshield

BOM

Category | Description | Qty | Comments
Sundries | Corrugated cardboard 190 x 210 x 6 | 1 | Cut from packaging
Sundries | Aluminium foil tape 50 x 226 x 0.5 | 1 | Supplied

Method

The heat shield reduces the heat radiating downwards from the bed. This helps the heat bed to warm up more quickly and reach a higher maximum temperature. The 6mm double-wall corrugated cardboard used for printer kit boxes is used as a cheap and effective insulator and aluminium foil tape on top reflects heat back towards the bed.

The shield can be retro-fitted but we find it is much quicker and easier to fit it as part of the main build.

Cut a piece of cardboard to the size given in the BOM hold it against the Y-carriage and cut a notch out of one long side to clear the ribbon cable clamps and a small notch to clear the front hex pillar.

Cut a piece of aluminium tape about 250mm long, peel off the tape backing and apply to the cardboard, wrapping the overlap underneath. Repeat with 4 more strips. We find it easiest to start with a central strip from the notch at the back to the front, then to add 2 more strips with about 5-10mm overlap on each side of the central strip. Fold the edge overlaps underneath.

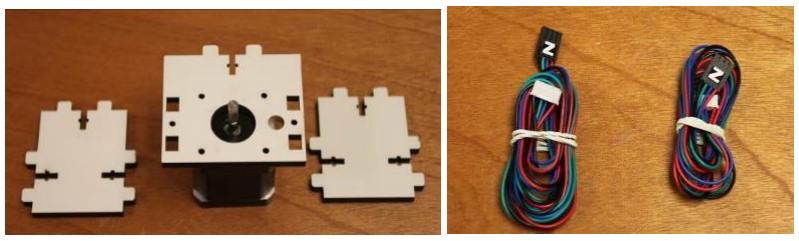
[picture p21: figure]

M90LC Manual | 24 of 70 | V0.4-20131016

### 10. Z-Axis Sub-Assemblies

Z-motors

BOM

Category | Description | Qty | Comments
MDF | Z-motor bracket top | 2
MDF | Z-motor bracket side | 4
Electrical | Z-motor cable L - 1.00m long | 1
Electrical | Z-motor cable R – 630mm long | 1
Mechanical | Stepper motor NEMA17 high-torque 44Ncm | 2
Fasteners | M3x12 socket cap screw | 8
Fasteners | M3x16 socket cap screw | 4
Fasteners | M3 form A flat washer | 12
Fasteners | M3 external shake proof (star) washer | 12
Fasteners | M3 square nut | 4

Method

1. Fit the motors to the top plates with the plugs at the back using four M3 x12mm screws, star washers and plain washers. Note that due to the slight angle of the laser cut the top plates have a “right” and a “wrong” side – the motor spigot will easily fit into the large circular hole the right way, but not the wrong way. If it doesn't want to go in, do not force it, turn the MDF plate over and try again.
2. Fit the sides to the top plates with M3 x16 socket cap screws, star and flat washers, and M3 square nuts in the nut traps.

Z motor boxes (already fitted to frame, which is done at a later stage)

3. Plug in the motor cables. The long cable is for the left-side motor, which can be identified by the position of the 8mm diameter hole for the smooth rod, which is on the right of the motor shaft.

M90LC Manual | 25 of 70 | V0.4-20131016

Z-top-brackets

BOM

Category | Description | Qty | Comments
MDF | Z-top brackets base | 2
MDF | Z-top brackets sides | 4
Fasteners | M3x16 socket cap screw | 4
Fasteners | M3 form A flat washer | 4
Fasteners | M3 external shake proof (star) washer | 4
Fasteners | M3 square nut | 4

Method

The brackets have two holes, one reamed to 8mm and one is a clearance hole for the 5mm lead screw, Ensure the brackets are aeesmbled one left handed (8mm hole on the left) and one right handed (8mm hole on the right). Note that it is possible to fit the triangular pieces the wrong way - the long edge of the triangle should be against the square piece so the edges line up.

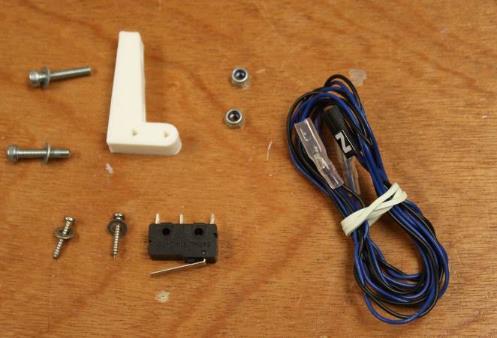
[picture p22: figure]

M90LC Manual | 26 of 70 | V0.4-20131016

Z-endstop

BOM

Category | Description | Qty | Comments
Electrical | Micro switch end stops | 1
Electrical | Z-endstop cable - 900 long | 1
Printed | z-top-limit-switch-bracket | 1
Fasteners | M3x16 socket cap screw | 2
Fasteners | M3 form A flat washer | 2
Fasteners | M3 nyloc nut | 2 | Pre-fitted
Fasteners | No 2 x 1/2 Pozi pan S/T screw | 2
Fasteners | M2.5 flat washer | 2

Method

1. Attach the micro switch to z-top-limit-switch-bracket with No 2 x 1/2 Pozi pan self-tapping screws, with the lever/blade of the switch facing as shown in the photo below.
2. Plug the spade connectors of the endstop cable onto the 2 outer terminals of the switch.
3. Screw the M3 x16 socket cap screws with star and flat washers a little way into the captive nuts to keep everything together until the endstop bracket is mounted as part of the Z axis assembly.

M90LC Manual | 27 of 70 | V0.4-20131016

### 11. Extruder Sub-Assemblies

E-motor

BOM

Category | Description | Qty | Comments
Electrical | Extruder PCB assembly | 1
Mechanical | Stepper motor NEMA17 high-torque 44Ncm | 1
Printed | d_motor_bracket | 1 | Pre fitted
Printed | d_motor_bracket_lid | 1
Printed | wades_small_gear | 1
Fasteners | M3X6 socket set screw | 1 | Pre-fitted
Fasteners | M3x45 socket cap screw | 2
Fasteners | M3 full nut | 2 | Pre-fitted
Fasteners | M3 square nut | 1 | Pre-fitted
Fasteners | M3 form A flat washer | 2
Fasteners | No 2 x 1/2 Pozi pan S/T screw | 2
Fasteners | M2.5 flat washer | 2

Method

Note that the cable plug on the motor is on top (right hand side of the motor in the diagram).

1. Insert the PCB into the pre-fitted D-motor-bracket, check that the two M3 nuts are in the nut traps and then screw down the lid pieces (which hold connector and the nuts in place) using No2 x 15mm pan self-tapping screws and M2.5 washers.

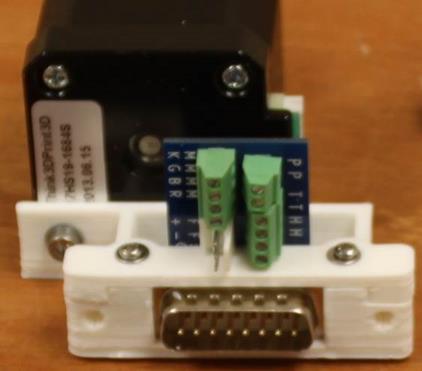
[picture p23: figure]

M90LC Manual | 28 of 70 | V0.4-20131016
2. Fit the gear to the motor leaving only a small gap between the gear and the motor. The grub screw needs to be tight to avoid working loose but not too tight or it will crack the plastic gear.
3. Plug in the motor cable and connect the loose ends to the terminals as follows: -
Terminal PCB Label | Motor Wire
MK | Black
MG | Green
MB | Blue
MR | Red

M90LC Manual | 29 of 70 | V0.4-20131016

Extruder

BOM

Category | Description | Qty | Comments
Electrical | J-head hotend assembly | 1
Mechanical | Round rail hardened and ground 22mm long | 1 | Pre-fitted
Mechanical | Bearing, ball, 608ZZ | 3 | Pre-fitted
Printed | wades_big_gear | 1
Printed | wades_block | 1
Printed | wades_gear_spacer | 1
Printed | wades_idler_block | 1
Sub-assembly E-motor | | 1
Fasteners | M3x10 socket cap screw | 3
Fasteners | M3x16 socket cap screw | 3
Fasteners | M3 form A flat washer | 3
Fasteners | M3 external shake proof (star) washer | 6
Fasteners | M3 full nut | 3 | Pre-fitted
Fasteners | M4x45 socket cap screw | 2
Fasteners | M4x20 hex set screw | 2
Fasteners | M4 form A flat washer | 7
Fasteners | M4 full nut | 2 | Pre-fitted
Fasteners | M8x60 hex bolt hobbed at 25 | 1
Fasteners | M8 external shake proof (star)washer | 1
Fasteners | M8 full nut | 2
Fasteners | Spring Flexo 93003, 11.34N/mm | 2

Extruder assembly parts (note that the 2 M4x50 hex head screws in the bottom right of the picture have been replaced with 2 M4x45 Socket cap screws, and the large spring by an M8 star washer)

M90LC Manual | 30 of 70 | V0.4-20131016

Method

1. Push the hot end into its socket so the wires come up the front of the wades block and slightly to the left.
2. Secure it in place with three M3 x 16mm cap screws with M3 star washers and M4 washers that capture the top of the groove, screwed into the pre-fitted captive nuts. The washers have to go in from the side before the screws go through them. Be careful to get the screws vertical to ensure they don't cross thread. It may be necessary to rotate the hot end to allow the screw heads to clear the zip tie. Ensure all the screws are in place before fully tightening them, this allows the extruder to be rocked/rotated to get them all in. Make sure it is aligned as shown before tightening the screws. Be careful not to overly flex the wires coming out of the hotend as they can break.
3. Place the M4 x 20mm bolts through their holes in the base of the block.
4. Loosely attach the motor with three M3 x 10mm socket cap screws, star and flat washers

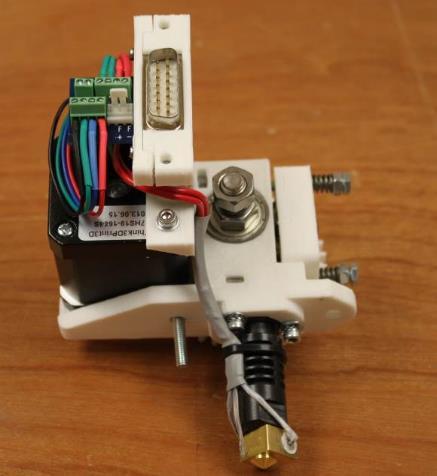
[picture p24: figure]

M90LC Manual | 31 of 70 | V0.4-20131016

trapping the M4 bolt below it in place. The 15 pin D type connector should be on the side closest to the bearings in the wades block (see picture below)

5. Pass all 4 of the wires from the hot end up past the motor underneath the PCB. Attach the red, hot end heater wires to the terminals marked H. (there is no polarity between these wires)
6. Attach the green thermistor wires to the terminals marked T. (there is no polarity between these wires)
7. Push the M8 hobbed bolt through the large gear and make sure it is fully seated. Add the spacer to the bolt and put the bolt through the bearing block. Ensure that the hobbed portion of the bolt is directly inline with the filament path. If it is not then the bolt may not be fully seated. Try pressing it in further or tighten an M8 nut on the other side of the bearing block to pull the bolt further in.
8. Slide the motor up to engage the gears and rotate them to ensure they don't bind or have too much backlash. Lock the motor in position by tightening the exposed socket cap screw. Remove the large gear and hobbed bolt and tighten the remaining screws.
9. Replace the hobbed bolt and gear and check the gears still correctly mesh. Secure with an M8 nut finger tight. Add the M8 star washer and second nut to lock it in place. Finger tight is generally enough to stop it shaking loose.
10. Put the springs with a washer on either side on the M4 x 45mm socket cap screws and thread them through the idler block into the bearing housing and into the trapped nuts. Tighten them until the screw head with the springs are compressed to 6mm measured between the washers.
11. Push some filament into the extruder hard against the hobbed bolt whilst turning the large gear to pull it in. Some force on the filament is needed initially to open the idler but once you see it open the filament can be fed by just turning the gear.
12. This is the way the extruder is loaded. Normally one would wind it in by hand until it hits some resistance, then heat the extruder and feed it with the motor. In this case just wind it up and down and check the gears don't bind. The spring force pushes the bolt a little further back in the bearings, so you might need to slacken off the motor a bit.

M90LC Manual | 32 of 70 | V0.4-20131016

### 12. Frame Assembly

BOM

Category | Description | Qty | Comments
MDF | Base | 1
MDF | Portal | 1
MDF | Left buttress | 1
MDF | Right buttress | 1
MDF | Roof | 1
MDF | Bowden extruder mounts - tabbed (optional) | 2
MDF | Bowden extruder mount - no tabs (optional) | 1
Printed | Alu_channel_caps | 4
Sundries | Alu channel 32x13x3, 449 long (handed) | 2
Sub-assembly Z-motors (handed) | | 2
Fasteners | M3x16 socket cap screw | 28
Fasteners | M3x20 socket cap screw | 4
Fasteners | M3x25 socket cap screw | 2
Fasteners | M3 form A flat washer | 38
Fasteners | M3 external shake proof (star) washer | 30
Fasteners | M3 nyloc nut | 4
Fasteners | M3 square nut | 30

Laser cut frame parts. (Note that the Z motor and top bracket parts are illustrated but it is easier if these are assembled as sub assemblies first - see the Z Axis Sub-Assembly section)

Method

All the laser-cut parts are held together with M3x16 socket cap screws fitted with star and flat washers, and screwed into square nuts fitted to the nut slots in the mating part. As previously noted, laser-cutting produces parts with a slightly tapered hole so if a square nut doesn't easily fit into its slot, try it from the other side.

The bolts only need to be tightened enough to compress the star washers partially. Excessive tightening will damage the captive nut holes in the MDF.

As indicated in the BOM, the Bowden extruder mount is optional as it is only required when upgrading to dual or multiple extruders. However, fitting it after the machine is

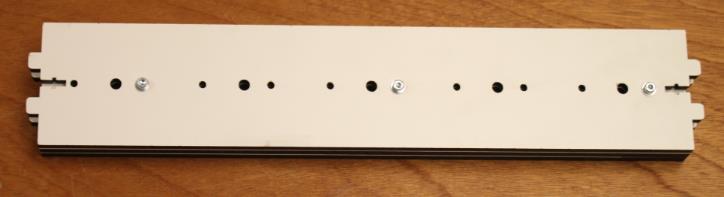
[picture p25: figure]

M90LC Manual | 33 of 70 | V0.4-20131016

built requires a complete strip down and rebuild, so we strongly recommend fitting it now.

1. Fit the Bowden extruder mount-no tabs between the 2 Bowden extruder mounts–tabbed, with all the bolt holes aligned, and fix together with 2 x M3x25 socket cap screws, washers and nyloc nuts in any of the holes. These may be left in place after assembly, or removed if needed as spares. Note that this “extruder sandwich” should be oriented as shown in the picture with the large holes slightly closer to the small holes on the right.
2. Lie the right hand buttress support (it has the most holes for mounting the electronics) on the table so the semi-circular notch is on the right to ensure it is the right way round. Slot the Bowden sandwich and the rear roof into their slots. The tabs on the rear roof should also face to the right. Secure these panels in place.
3. Fit the left-hand buttress to this assembly and secure in place. The semi-circular notch should line up with the right hand side.

M90LC Manual | 34 of 70 | V0.4-20131016

=>

4. Identify the front and back of the portal – the wider leg is on the right when looking at the front. Fit the portal to the front of the buttress-assembly and secure in place. To make securing it easier, slide the nuts into their traps before attaching the portal.
5. Identify the left and right Z-motor bracket sub-assemblies - the rod-holes are inside the motor shafts, towards the centre of the machine. Fit the motor-bracket assemblies to the front of the portal, feeding the cables through the holes provided.

M90LC Manual | 35 of 70 | V0.4-20131016
6. Use the semi-circular holes in the buttresses to keep the Z Motor cables neat while completing the remainder of the assembly.
7. Turn the assembly upside-down and fit the base after identifying the correct way up and fitting square nuts in all the nut traps. Try not to bump the assembly to avoid knocking nuts out. Align the tabs on one side first, then the other. Do not apply excessive force but you may need to gently flex the frame so the tabs line up.

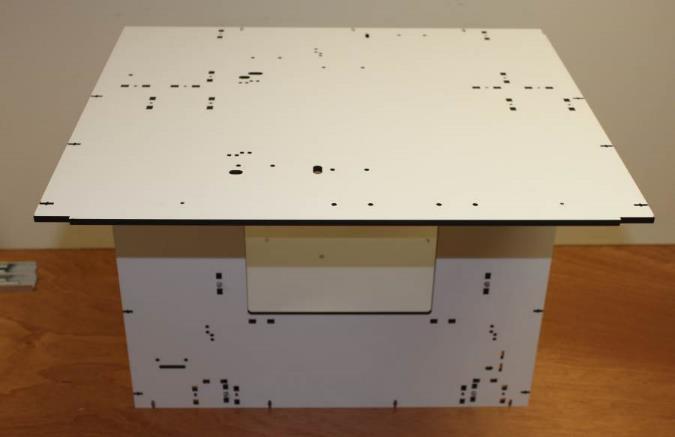
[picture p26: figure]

M90LC Manual | 36 of 70 | V0.4-20131016
8. Fit bolts to the holes which lead to nut traps in the portal and Z-motor-brackets, but not the left and right hand buttresses. This is to allow for the aluminium base channels to be added in the next step
9. Line up the aluminium base channels with the buttress holes. They are drilled to fit left and right with two holes at the back for the buttress M3x20 screws, the large hole for the head of the portal screw towards the centre of the machine, and a single hole at the front for an M3x16 socket cap screw. Fix the base channels through the base into the 4 square nuts in the buttresses with M3x20 socket cap screws, but do not tighten fully. Fit the M3x16 socket cap screws with washers inserted from the top of the base through the front end channels and secured with M3 nyloc nuts and washers in the channels, left loose for now.
10. The bolt-holes in the channels are large enough to allow the channels to slide backwards and forwards a little. Push the channels all the way to the back of the machine to align with the rear edge of the frame base, then tighten all the bolts. The Alu_Channel_Caps can be fitted now but they are best left to the end as the frame will be moved around during the remainder of the assembly process.

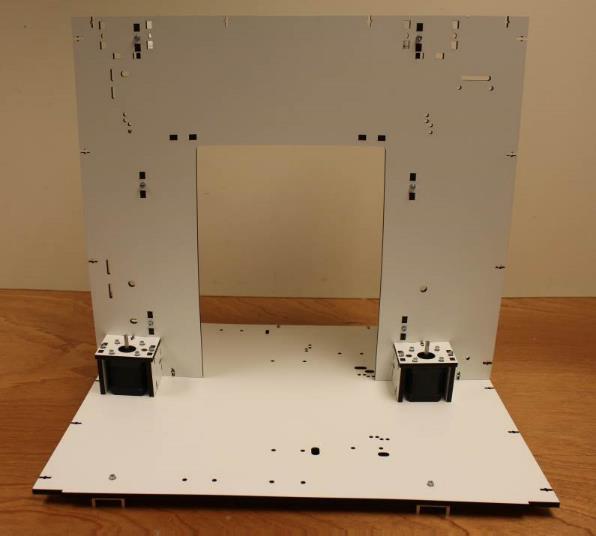
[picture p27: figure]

M90LC Manual | 37 of 70 | V0.4-20131016
11. The frame assembly is complete, now move onto the Y Axis Assembly.

M90LC Manual | 38 of 70 | V0.4-20131016

### 13. Y-Axis Assembly

BOM

Category | Description | Qty | Comments
Electrical | Heatbed wiring loom | 1
Electrical | Micro switch end stops | 1
Electrical | PCB heatbed Mk2a assembly | 1
Electrical | Y-endstop cable - 950long
Fasteners | M2.5 flat washer | 2
Fasteners | M3 External Shake proof (star) Washer | 3
Fasteners | M3 Form A Flat Washer | 8
Fasteners | M3 Form A Flat Washer | 4
Fasteners | M3 Full Nut | 3
Fasteners | M3 Nyloc Nut | 2
Fasteners | M3 Nyloc Nut | 4
Fasteners | M3x10 Socket Cap Screw | 3
Fasteners | M3x16 Socket Cap Screw | 3
Fasteners | M3x16 Socket Cap Screw | 4
Fasteners | M3x20 Hex PCB spacer F/F chromed brass | 3
Fasteners | M3x20 Socket Cap Screw | 2
Fasteners | M4 Form A Flat Washer | 10
Fasteners | M4 Nyloc Nut | 10
Fasteners | M4x20 Socket Cap Screw | 10
Fasteners | No 2 x 1/2 Pozi Pan S/T screw | 2
Mechanical | Round rail hardened and ground 274mm long (Y) | 1
Mechanical | Round rail hardened and ground 417mm long (Y) | 1
Mechanical | T2.5 timing belt Y=668mm | 1
Printed | ribbon_clamp_26_33 | 1
Printed | ribbon_clamp_26_33N | 1
Printed | ribbon_clamp_26_44N | 1
Printed | y_bar_clamp | 3
Printed | y_bar_clamp_switch | 1
Sub-assembly | Print-bed | 1
Sub-assembly | Y-carriage | 1
Sub-assembly | Y-heatshield | 1
Sub-assembly | Y-idler | 1
Sub-assembly | Y-motor | 1
Sundries | Bulldog clip 19mm | 1
Sundries | Glass sheet 214 x 202 x 3, 2x10x10 chamfer | 1
Sundries | Polypropylene strip 270 x 33 x 0.5 | 1

M90LC Manual | 39 of 70 | V0.4-20131016

Sub Assemblies

Method

Y axis assembly (note the heatbed and heat shield are not shown)

1. Insert the M3x16mm socket cap screws in each of the Y bar clamps so they engage with the pre-fitted captive nyloc M3 nuts.
2. Turn the machine onto its side. Loosely fit the two left hand Y bar clamps to the base with the M4 x20mm socket cap screws, oriented so the slits in the clamps are towards the inside of the machine. Carefully insert the long Y-rod to line up the brackets, using a gentle twisting motion.. Tighten the fixing bolts through the machine base but do not tighten the M3 clamping bolts, then remove the rod.

M90LC Manual | 40 of 70 | V0.4-20131016
3. Plug the spade connectors of the green-and-black Y-endstop cable onto the Y-endstop micro switch, bending the bottom connector downwards at an angle. Screw it to the y_bar_clamp_switch with No2 pozi pan self-tapping screws and M2.5 washers with the button towards the top and facing the back of the machine.
4. Fit the right hand Y bar clamps to the base but leave the screws loose enough that the clamps can move during the alignment in step 13.

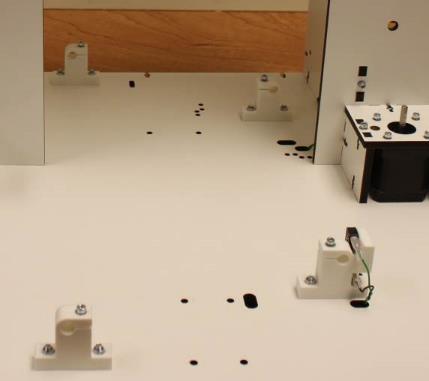
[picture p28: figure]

M90LC Manual | 41 of 70 | V0.4-20131016
5. Plug in the Y motor cable, thread the Y motor wires through the hole in the base and then screw the Y motor bracket securely in place.
6. Thread the Y limit switch and motor cables through the cable ties, along the underside of the base through a second cable tie, up through the hole in the base and then through the adjacent hole in the right buttress as shown below.
7. Fit M3 x 16 socket cap screws from below to the 2 back corner holes and central front hole of the Y carriage, using star washers and flat washers underneath and flat washers and full nuts above. Tighten firmly but do not over tighten as the MDF is slightly compressible. Add an extra washer on top of the nut on the 2 rear bolts and screw the pillars down firmly at the back.
8. Screw the front pillar down to the same height by using a washer as a temporary shim (don’t slide it onto the bolt but rest it on the nut so it is pinched by the hex pillar). The front pillar is used to level the bed relative to the nozzle in the Y-direction (front-to-back), this washer, acting as a shim, sets it close to correct as a start point. Any difference in level in the X-direction is corrected on the Z-axis lead screws, not on the heat bed.
9. Clamp the Y belt (the shorter of the two) in the front belt anchor with the teeth facing away from the carriage. The end of the belt should project enough to have four complete teeth showing.

M90LC Manual | 42 of 70 | V0.4-20131016
10. Put a half twist in the belt and the thread it through the Y idler assembly with the smooth side against the bearings and then clamp it in the rear clamp with the teeth facing the carriage. Again leave four complete teeth projecting from the anchor.
11. Slide the left Y bar through the bar clamps and the carriage bearings, using a gentle twisting motion to avoid knocking balls out of the bearings. Tighten the clamps to grip the bar lightly but do not over-tighten them
12. Repeat the process for the right bar, then slide the carriage up and down to align the right hand bearing and bar clamps. Tighten the bearing first and then move the carriage to each end and tighten the clamps.
13. Put the belt over the motor pulley and fasten the idler assembly to the base with enough tension on the belt to play a low note when plucked. Ensure the belt runs in the middle of the idler without touching the washers each side by adjusting the angle of the idler. Similarily the position of the pulley on the motor shaft may need to be adjusted slightly.
14. Lay the heat bed cable loom (ribbon-cable) on the y carriage as shown, using M3 x 20mm screws and washers, clampit together with the polypropylene strip (which goes closest to the clamp) to the y carriage with the ribbon_clamp_26_33 and ribbon_clamp_26_33N.

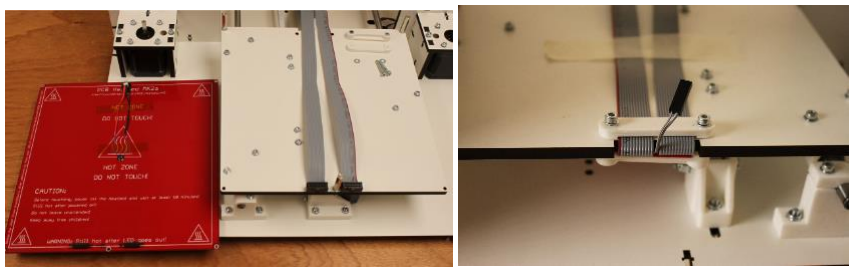
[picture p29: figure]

M90LC Manual | 43 of 70 | V0.4-20131016
15. Lay the heat shield on the Y carriage with the notch at the back between the underside of the bed and the cable. The heat shield can be taped into place as shown with short pieces of the supplied aluminium tape.
16. Plug the two 6x2-way IDC connectors on the bed end of the bed ribbon cable onto the 6x2-pin headers soldered to the front edge of the heat bed and plug the thermistor connector onto the white 2-pin header stuck to the back of the heat bed. Screw the bed to the top of the pillars with the M3 x 10 socket cap screws (no washers).

M90LC Manual | 44 of 70 | V0.4-20131016
17. The ribbon cable and polypropylene strip route towards the front of the printer under the y axis before doubling back. Clamp the bed's ribbon cable and polypropylene strip to the base with the ribbon_clamp_26_44N. The wires turn right and go through the cable ties and under the holes in the right hand stay. The heater wires go through the rear tie and the larger hole

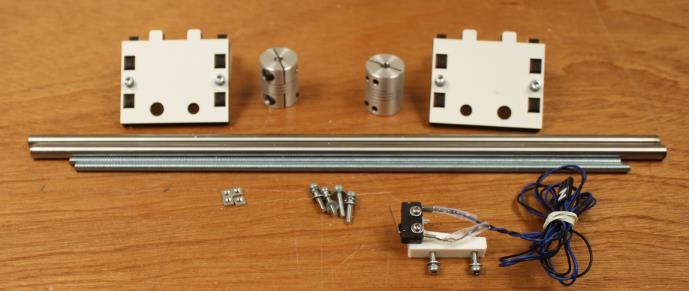
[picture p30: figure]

M90LC Manual | 45 of 70 | V0.4-20131016

### 14. Z Axis Assembly

BOM

Category | Description | Qty | Comments
Mechanical | Round rail hardened and ground 344mm long (Z) 2
Sub-assembly Z-top-bracket assemblies | | 1
Sub-assembly Z-endstop assembly | | 1
Sub-assembly Y-idler | | 1
Sub-assembly Y-motor | | 1
Fasteners | M3x16 socket cap screw | 4
Fasteners | M3 form A flat washer | 4
Fasteners | M3 external shake proof (star) washer | 4
Fasteners | M3 square nut | 4

(Note that the threaded rod and couplings are used in the next section)

(Note that the cable loom is gathered together for the photograph only)

Method

The X motor and idler sub-assemblies form the interface between the X and Z axis. They are part of the X axis but are assembled with the Z axis.

1. Fit the Z top endstop and feed the cable through the hole. It is routed alongside the z-motor wires and zip tied into place. The endstop is best fitted in the centre of the slot range to start with, it will be adjusted later.
2. Fit the Z-top-brackets to the front of the portal with M3 x16mm socket cap screws, washers and square nuts, with the 8mm holes for the Z-rods facing inwards towards the centre of the machine. Tighten the bolts to keep the brackets steady for the next step

M90LC Manual | 46 of 70 | V0.4-20131016
3. Gently slide the smooth rods through the top brackets and partway down towards the Z-motor brackets. They are a tight fit so work slowly, supporting the brackets. If they will not move then twist gently as you push but do not be tempted to hammer them or use excessive force.
4. Once the rods are partway down, insert them through the X-ends with the idler on the left and the motor box on the right. Twist the rods gently to avoid knocking out the balls out of the linear bearings, then push them all the way down into the matching holes in the Z-motor brackets.
5. Slacken off the Z-top-brackets fixing screws just enough to allow them to move slightly when the X-axis is fitted.

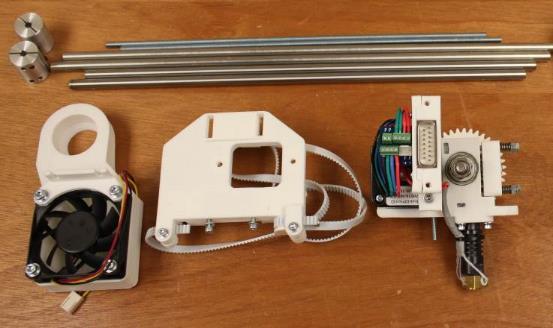
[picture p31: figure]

M90LC Manual | 47 of 70 | V0.4-20131016

### 15. X-Axis assembly

BOM

Category | Description | Qty | Comments
Mechanical | Round rail hardened and ground 381mm long (X) | 2
Mechanical | M5 threaded rod lead screws 305 long | 2
Mechanical | Beam couplings 5mm/5mm | 2
Printed | ribbon_clamp_20_44N | 1
Printed | ribbon_clamp_20_44 | 1
Sub-assembly X-carriage | | 1
Sub-assembly X-carriage-fan | | 1
Sub-assembly Extruder | | 1
Fasteners | M4 nyloc | 2 | Pre fitted
Fasteners | M4 Flat washer | 2
Fasteners | M4x20 socket cap screw | 2
Fasteners | M4 Wing nut | 2

Note the shorter smooth rods shown in the picture above have already been fitted as part of the Z axis assembly
Method
1. Put the X ends at the bottom of the Z axis. Make sure the X bars are free of grease to help the clamps to grip. Remove the idler's axle bolt.

M90LC Manual | 48 of 70 | V0.4-20131016
2. Slide the X bars through the idler bracket, the X carriage and into the motor bracket as far as they will go. Take care when passing the rods through the X carriage bearings, twisting them to ensure no ball bearings are knocked out. You may find it helpful to support the carriage, for example by using the empty power supply box.
3. Tighten the X bar clamps while the axis is at the bottom. Tighten the 4 cap screws of each bar clamp evenly in a criss-cross pattern. Don't over tighten them, i.e. tighten just enough until you feel the clamp grips the bar solidly.
4. Put the belt round the motor pulley and then re-attach the idler axle with the belt around the idler.
5. Tension the belt enough to play a low note when plucked.
6. Run the carriage side to side a few times and check that the belt does not rub on

M90LC Manual | 49 of 70 | V0.4-20131016

the edge of the pulley. If it does, slightly adjust the position of the motor pulley so that it runs true.

7. Move the axis to the top and then tighten the Z-top-brackets. The axis is now aligned top and bottom. Move the X-axis up and down the Z rods a few times to confirm it runs smoothly. If it does not then use the slight play in the Z-top brackets when the screws are slackened to allow it to run smoothly
8. Pass the connectors at the end of the X Motor and Extruder loom through the slot on the right hand side of the portal and fix the loom in place with the ribbon_clamp_20_44N on the front and the ribbon_clamp_20_44 .on the back. Form the loop using the polypropylene strip, this is best done with the carriage half way up the Z axis. .
9. Fit the beam couplings to the Z-motors with the motor shaft projecting no futher than half way through the coupling, and tighten the grub screws. It may be helpful to use a piece of cardboard or similar as a spacer to ensure the couplings are the same distance from the top of the motor. Once again supporting the X axis out of the way using the power supply box makes this process easier. Tighten the clamp bolts to take up the slack. There is no need to apply excessive force to tighten these to the motor shaft.
10. Lower the x axis to heat bed. Insert the M5 lead screws through the holes in the top brackets, drop them down to the X-ends and screw them through the pre-fitted M5 nuts.
11. Continue to thread the lead screws down into the top of the beam couplings, once they are all the way to the top of the motor sharft, back them up 2 full turns to ensure there is a gap to allow the couplings to flex. Tighten the beam coupling clamp bolts first, as tight as possible, then tightening the grub screws as well.

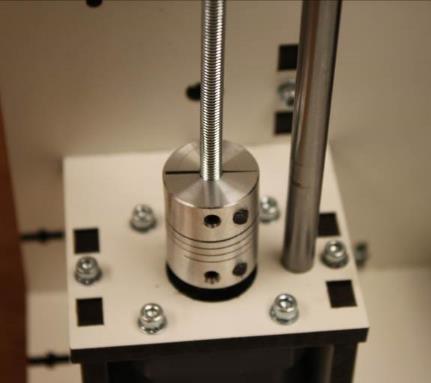
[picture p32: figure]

M90LC Manual | 50 of 70 | V0.4-20131016
12. Slot the extruder into place with the gears closest to the portal and secure it with the M4 wing nuts, ensure the hotend cable does get pinched by the gap between the X-carriage and the extruder body. If the right hand wing nut stops in a position where it sticks out beyond the carriage try the hex head in a different one of the six possible positions.
13. Mate the D type connectors and screw the captive M3 screws in the shell into the captive M3 nuts in the d_motor_bracket. Do not over tighten them.

M90LC Manual | 51 of 70 | V0.4-20131016

### 16. Electronics Assembly

BOM

Category | Description | Qty | Comments
Electrical | RAMPS1.4 | 1
Electrical | Arduino Mega 2560 compatible board | 1
Electrical | Blue Stepsticks with loose heatsinks | 5
Electrical | Panelolu2 LCD controller with RAMPS1.4 adaptor | 1
Electrical | PSU ALPINE 600 assembly | 1
Electrical | IEC PC PSU mains lead with moulded-on plug | 1
Electrical | Micro SD card | 1
Electrical | Micro SD to USB adapter | 1
Electrical | USB A to B lead x 1.5m long | 1
Printed | ATX_PSU_bracket short | 1
Printed | ATX_PSU_bracket long | 1
Fasteners | M3x10 socket cap screw | 7
Fasteners | M3x16 socket cap screw | 3
Fasteners | M3 form A flat washer | 7
Fasteners | M3 external shake proof (star) washer | 7
Fasteners | M3x20 Hex PCB spacer F/F chromed brass | 3
Fasteners | M4x20 socket cap screw | 4
Fasteners | M4 form A flat washer | 6
Fasteners | M4 external shake proof (star) washer | 2
Fasteners | M4 nyloc nut | 4 | Pre-fitted
Fasteners | 6-32 x 1/2 pan screw | 2

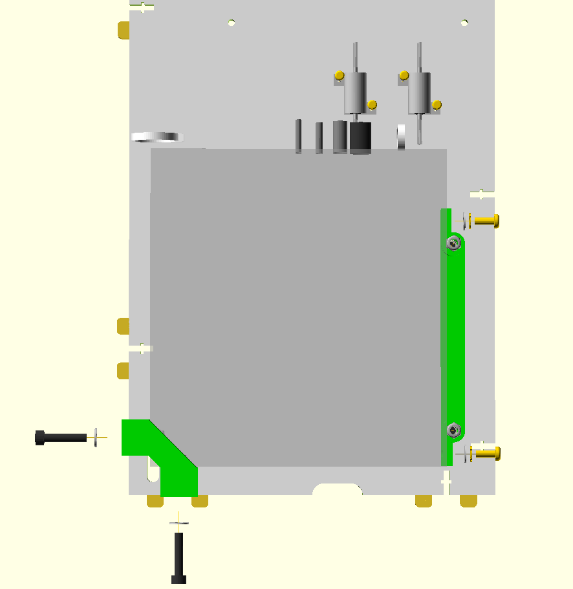
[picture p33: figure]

M90LC Manual | 52 of 70 | V0.4-20131016

Method

1. Turn the frame onto its left side so the electronics bay is on top and facing towards you. Be careful that the x or y carriage don’t crash from end to end while turning it around.
2. The M4 nyloc nuts are pre-fitted in the nut traps of the two brackets. Loosely screw the brackets to the frame with M4 x 20mm socket cap screws and flat washers. The long bracket runs vertically close to the back with the tall lug at the base. The small bracket joins between the base and portal so the smooth flat side is on top as you see it. The brackets are designed to provide a slot for the power supply to fit into.
3. Run the wires from the right Z motor, the Y motor, the Y endstop and the bed up the corner between the portal and the right buttress before fitting the PSU between the brackets.

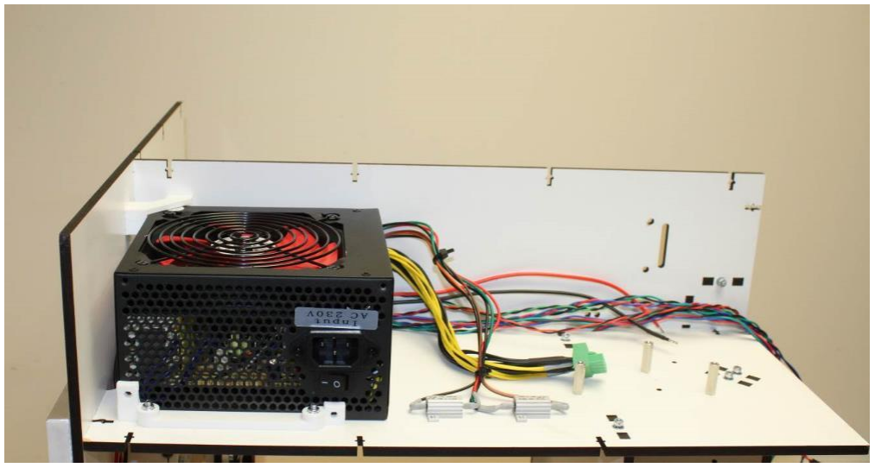
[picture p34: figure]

M90LC Manual | 53 of 70 | V0.4-20131016
4. The PSU is aligned so the fan faces up and the switch is to the back. Check no wires are trapped underneath the PSU then secure it into place with two 6-32 x 1/2 pan screws, M4 star washers and M4 flat washers. Tighten the brackets holding the PSU to the frame.
5. The resistor lugs are tapped M3. Fix the resistors to the frame using four M3 x 10mm socket cap screw screws, star washers and flat washers (The resistor locations have changed slightly since the picture was taken). Insert the screw from the other side of the frame using the resistor lug as the nut.

IMPORTANT NOTE. The Arduino + RAMPS + Stepsticks combination forming the electronic controller can be damaged if the wiring is incorrect, or by failure to observe antistatic precautions when handling. The controller is supplied loaded with Marlin firmware configured for the Mendel90 with Panelolu LCD panel, and has had a full functional test with the actual wiring looms and cables, motors, limit switches, hotend, heatbed and fan supplied in the kit.

6. Fit the hex pillars to the buttress with three M3x16 socket cap screws, star and flat washers from behind (underneath with the machine on its' left side). Use the picture to identify the correct holes.
7. Fit the Arduino vertically so the USB socket points towards the PSU to the tops of the hex pillars with M3x10 socket cap screws without washers securely but not over tight.

M90LC Manual | 54 of 70 | V0.4-20131016
8. Fit the RAMPS to the Arduino, making sure all the pins line up.
9. Connect up all the wiring, referring to the RAMPS wiring schematic (http://reprap.org/mediawiki/images/6/6d/Rampswire14.svg) if uncertain. Careful routing of some of the cables under the board will make the finished job look much tidier and the cables can be grouped together with cable ties.
- Green power plug from PSU into green 4-way RAMPS socket
- Heatbed power cables into RAMPS D8
- Extruder power cables into RAMPS D10
- Fan single wire into GND terminal of RAMPS D9
- Ribbon cable wires (all labelled) onto X-motor, E-motor, X-endstop (red to outside), and E-thermistor.
- Y- and Z-motors and end stops and heatbed thermistor
- Ensure end stops are connected between S and GND(coloured wires towards the outside)
10. Fit Panelolu 2 ribbon cable and Panelolu2
11. Attach the USB cable, which will be used along with your PC during calibration of the printer.

This concludes the assembly process prior to commissioning and calibrating your printer. The X-carriage fan assembly is best fitted after calibration. If you are fitting the optional acrylic cabinet then this is also best done after calibration, and is covered in a separate section later in this manual.

M90LC Manual | 55 of 70 | V0.4-20131016

### 17. Firmware and Software

The micro SD card with the kit comes preloaded with software to operate the machine on Windows (Linux versions of all the tools are available online). Please copy the files from the SD card to somewhere safe on a computer.

After this has been copied to your PC the card can be wiped and used with the Panelolu2 to run the machine. Running G code from the card gives more consistent results than sending it over USB. A USB SD card reader is included in the kit to allow G-codes to be loaded to the card from your PC. Once the machine is fully calibrated you should be able to control prints entirely with the Panelolu2, without having to attach the PC again. There is a command tree in the Marlin directory (LCD Menu Tree.pdf) which shows the controls available.

The following programs are included: -

Marlin Firmware

This is the source code for the firmware that is pre-loaded on the Arduino and is located in the directory Marlin_T3P3_M90LC_v0_7. It is our fork of Marlin with Panelolu2 support and is also available on GitHub at https://github.com/T3P3/Marlin. The pre-installed version is sufficient to test the machine but calibration will be required, which involves tweaking the Z axis height and the hobbed bolt diameter.

Arduino IDE

This is used to compile and load the firmware and is located in the arduino-0023 directory Once copied to your PC it can be run simply by clicking on arduino.exe, as no installation is needed. It can also be downloaded from http://arduino.cc/en/Main/OldSoftwareReleases. Although not the latest version of Arduino, it has been thoroughly tested for Marlin uploads and is very reliable.

When started it opens an empty sketch. Use the File/Open menu to navigate to Marlin_T3P3_M90LC_v0_7\Marlin_T3P3_M90LC_v0_7.pde and click on it. Marlin opens in a new page. Click on the configuration.h tab and:

1. Find Line 306 “#define Z_MAX_POS 210”. This will need to be changed to the actual Z-height in mm as determined by calibration (described in the next section of this manual).
2. Find Line 328 “#define DEFAULT_AXIS_STEPS_PER_UNIT {80,80,3200/0.8,520} “. The last number 520 is the extruder steps in mm. This will need to be confirmed by calibration.

When you are directed below to update the firmware do the following: -
- Use the Tools / Board menu option to set the board to “Arduino Mega 2560”.
- Use the Tools / Serial Port option to select the correct USB port.
- Press the play button.
- Wait for”Done uploading” to appear.
- Save your changes with the save button.
Pronterface

This is a host application used to control the printer downloaded from http://koti.kapsi.fi/~kliment/printrun/ and is located in the directory Printrun-Win-Slic3r-12July2013.

Again it needs no installation. Simply copy the folder to hard disk and run Printrun-Win-

M90LC Manual | 56 of 70 | V0.4-20131016

Slic3r-12July2013\pronterface.exe.

Slic3r

This is the software used to produce G-code print files from the STL files produced by CAD programs. Download the latest version of Slic3r from http://slic3r.org/. The current version at the time of writing is also stored on the uSD card supplied with your kit.

Help on using Slic3r is available on the Slic3r website at http://manual.slic3r.org/. We supply the basic settings for the M90LC as a configuration file (M90LC_default_PLA_config.ini) on the uSD card.

M90LC Manual | 57 of 70 | V0.4-20131016

### 18. Testing and Commissioning

Power up

Plug in the mains and switch on the PSU. The PSU fan should run, and the Panelolu2 display should come to life. Connect the USB lead to a PC and a USB connection should appear. The Arduino board comes with Marlin installed and configured for 250kB.

Open Pronterface, set the baud rate and serial port and press “Connect”. After a few seconds the following should be displayed.

Connecting...
start
Printer is now online.
Marlin 1.0.0
echo: Last Updated: Oct 8 2013 08:22:09 | Author: (T3P3, M90LC v0.7)
20130925
Compiled: Oct 8 2013
echo: Free Memory: 4340 PlannerBufferBytes: 1232
echo:Hardcoded Default Settings Loaded echo:Steps per unit:
echo: M92 X80.00 Y80.00 Z4000.00 E520.00 echo:Maximum feedrates (mm/s):
echo: M203 X300.00 Y300.00 Z3.20 E45.00
echo:Maximum Acceleration (mm/s2):
echo: M201 X1000 Y1000 Z10 E45
echo:Acceleration: S=acceleration, T=retract acceleration
echo: M204 S1000.00 T3000.00
echo:Advanced variables: S=Min feedrate (mm/s), T=Min travel feedrate (mm/s), B=minimum segment time (ms), X=maximum XY jerk (mm/s), Z=maximum Z jerk (mm/s), E=maximum E jerk (mm/s)
echo: M205 S0.00 T0.00 B20000 X20.00 Z0.40 E5.00
echo:Home offset (mm):
echo: M206 X0.00 Y0.00 Z0.00
echo:PID settings:
echo: M301 P38.60 I4.55 D81.79
echo:SD init fail

Reading through this list you will see that it tells you what most of your Marlin configuration.h settings are. This can be useful when configuring a new version of Marlin before upload, if you forgot to save the last Marlin upload.

Limit switches

Check that the limit switches are working by typing M119 in the test box at the bottom right corner of the Pronterface window. When no switches are triggered they should all read low:

SENDING:M119
Reporting endstop status
x_min: open
x_max: open
y_min: open
y_max: open
z_min: open
z_max: open
Check that manually triggering each switch causes the corresponding input to change from open to TRIGGEREDH while the switch is held down. Also check that each axis is able to hit its limit switch. For X the extruder wing nut can get in the way. If this is the case simply rotate the hex head bolt in its socket. The Z axis must be reasonably level side to side so that the right hand side doesn't hit the top of the axis before the left side hits the limit

M90LC Manual | 58 of 70 | V0.4-20131016

switch. The micro-switch must be mounted in the correct orientation for the lever to strike its intended target (X with the lever hinge towards the top , Y towards the top, Z towards the back).
Motors

Put some lubricant on the X,Y and Z smooth rods and the Z lead screws and lithium grease on the extruder gears. ABS gears will run continuously for months with grease but wear out more quickly when run dry.

Move all of the axes manually to somewhere near the centre. Then check that all the axes move in the right direction by using the jog buttons in Pronterface. Click on the “10” ring in the +X quadrant and check that the carriage moves 10mm towards the right, towards the limit switch.. Since the limit switches have been verified to be working and the motor is running in the right direction it is now safe to home by pressing the X home button (house icon with an X).

Repeat the procedure for the Y axis. +Y moves the bed towards the switch.

Check the extruder feeds forwards when the “Extrude” is pressed and backwards when the “Reverse” button is pressed. Marlin will prevent you from doing 'cold extrusion'; you can override this with command M302, then try the extrude again. Make sure you don't have any filament loaded during this test.

Heaters

Tick the “Monitor Printer” to show the temperature graph. The figures under the “Check Temp” button should show the hot end (T) and the bed (B) to be around room temperature.

Set the “Heater:” target temperature to 220˚C and press the “Set” button. The temperature of the hot end should rise and settle at 220˚C. If you have a thermocouple probe you can insert it inside the hot end and verify the temperature at this stage (before the barrel is filled with plastic). To do this you will need to remove the idler and stiffen the thermocouple wire by sleeving it with about 150mm of PTFE tubing with an outside diameter less than 3mm.

Pressing the blue “Off” button should cause the temperature to slowly fall back to room temperature again.

Repeat the same procedure with the bed heater by setting it to 60˚C.

M90LC Manual | 59 of 70 | V0.4-20131016

### 19. Calibration

Firmware setup

The standard supplied firmware is already set up for the M90LC. The following lines within configuration.h are different from the default version of Marlin.

#define STRING_CONFIG_H_AUTHOR "(T3P3, M90LC)" // Who made the changes.

#define MOTHERBOARD 33

#define TEMP_SENSOR_0 5

#define TEMP_SENSOR_1 0

#define TEMP_SENSOR_BED 12

const bool X_ENDSTOPS_INVERTING = false; const bool Y_ENDSTOPS_INVERTING = false; const bool Z_ENDSTOPS_INVERTING = false;

#define DISABLE_Z true

#define INVERT_X_DIR false

#define INVERT_Y_DIR false #define INVERT_Z_DIR false #define INVERT_E0_DIR false

#define X_HOME_DIR 1

#define Y_HOME_DIR 1

#define Z_HOME_DIR 1

// Travel limits after homing

#define X_MAX_POS 200

#define X_MIN_POS 0

#define Y_MAX_POS 200

#define Y_MIN_POS 0

#define Z_MAX_POS 210

#define Z_MIN_POS 0

And we will set the Z axis height accurately in a later step

//leave commented out!
//#define MANUAL_HOME_POSITIONS

#define HOMING_FEEDRATE {30*60, 30*60, 3.3*60, 0}

#define DEFAULT_AXIS_STEPS_PER_UNIT | {80,80,3200/0.8,520}

#define DEFAULT_MAX_FEEDRATE | {300, 300, 3.3, 45} | // (mm/sec)

#define DEFAULT_MAX_ACCELERATION | {1000, 1000, 5, 45}

#define DEFAULT_ACCELERATION | 1000

#define DEFAULT_RETRACT_ACCELERATION 3000

#define EEPROM_SETTINGS

#define EEPROM_CHITCHAT

//if you have one plugged in #define PANELOLU2

Nozzle-bed alignment 1 – X axis levelling

1. If you have fitted the extruder fan, then remove it for this stage of the calibration. Fit the heatbed glass if not already done
2. Connect to the printer using Pronterface
3. Centre the X carriage on the x axis then home the Z axis in Pronterface by clicking

M90LC Manual | 60 of 70 | V0.4-20131016

on the Button with Z and a picture of a house.

4. Click “Disable Motors” in Pronterface and then manually move the X and Y axis so that the nozzle is in the left most (minimum) position on X ( X=~0) and almost to the maximum on Y, just clearing the bull dog clips (remember Y axis is described with reference to the nozzle, not the bed so with the nozzle at the top of Y, the bed is all the way forward).
5. Using the Z +/- buttons in Pronterface move the Z axis so that the nozzle is nearly touching the bed. Use a sheet of paper as a feeler gauge to check the nozzle height. While moving a sheet of paper under the nozzle, lower the Z axis until the paper just begins to drag against the nozzle. Be careful not to push down on the bed when using the paper as a feeler gauge.
6. Use the Z+1 button to lift the nozzle slightly above the paper and bed and then move the X carriage all the way to the right most (maximum) position (X=~200). Once in this position use the Z-1 button to drop the extruder back to the position it was at on the other side.
7. Click “Disable Motors” in Pronterface then, while holding the left Z coupling still with one hand adjust the right side of the X axis up or down using the right coupling until a piece of paper just drags under the nozzle. This is the first iteration done, however because the Z axis rods are further out then the edge of the bed we need to go through this process a number of times until no further adjustment is needed.
8. At this point use the Z+1 button in Pronterface to move the X axis up by 1mm, then move the x axis all the way across to the other side and repeat steps 5 to 7 until there is no difference in height between either side of the X axis.
9. The next step is to adjust the bed to be level on the Y axis.

Nozzle-bed alignment 2 – Y axis levelling

1. Ensure the X axis levelling step is completed then move the X-Axis so the nozzle is in the centre on X and almost all the way to the maximum on Y (i.e. the bed is all the way forward)
2. Move the nozzle down until it just drags on the paper used as a feeler gauge, as in the X axis levelling. Once again be careful not to push down on the bed when using the paper as a feeler gauge.
3. Use Z +1 to lift the nozzle from the bed slightly, then move the Y axis so the bed is all the way back. Use Z-1 to return the nozzle to the height it was at the other end of the Y axis. The nozzle should be just on the paper feeler gauge at the front.
4. In adjustment is required (ie the nozzle does not touch the paper or the paper is pushed down onto the bed, loosen the top screw on the bed mount hex pillar at the front slightly and then turn the hex pillar to raise or lower the bed slightly until the paper just drags on the nozzle. Tighten the top screw and confirm the paper still just touches the nozzle.
5. Use Z+1 to lift the nozzle slightly, return the bed all the way to the back.
6. Repeat above steps until there is no adjustment required between the front and back of the Y axis.

Setting the Z axis dimension

1. If not already connected, connect to the printer using Pronterface and set the bed and nozzle temperature to the desired printing temperature (135 bed, 250 extruder for ABS, 80 bed, 200 extruder for PLA). Z-height calibration should be done with

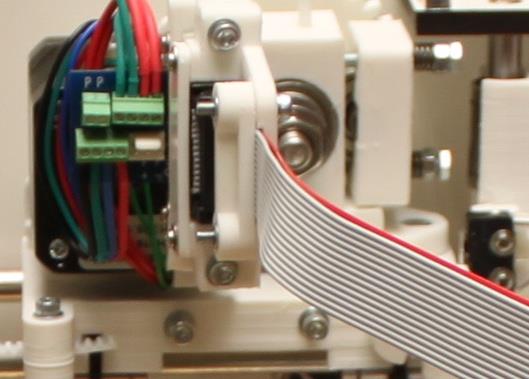
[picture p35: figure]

M90LC Manual | 61 of 70 | V0.4-20131016

everything at the printing temperature. Care should be taken not to touch the hot surfaces during this process.

2. Centre the X carriage in the X axis, then home the Z axis. Once the Z axis is at the top check for fouling at the Z motor ends as at Z-Max position. If there is still clearance and you wish to have maximum Z height then the Z endstop can be raised in the slot slightly, before being re-tightened. Similarly if there is fouling then the Z endstop can be lowered in its slot slightly to ensure the extruder clears the Z top Brackets with the X carriage all the way to the right. Re center the carriage on X and home Z between any endstop adjustments.
3. Type M114 to show the current X, Y and Z points, which should be X 200, Y 200, Z 210 if you are using our default version of marlin distributed with the kit.. Record the Z figure as Z_original.
4. Move the X carriage to the centre of the X axis and the Y carriage to the centre of the Z axis so the extruder is over the centre of the bed.
5. Type G1 Z20 to move the extruder to just above the bed, then use the Z- buttons in Pronterface to lower the extruder until just catches on a piece of paper, used as a feeler.
6. Type M114 again. This will show the current Z position. Record this as Z_error
7. | 7. | Now you know Z_original was too big by Z_error, so subtract Z_error from
Z_original and you have the correct Z-height within a sheet of paper. Add 0.1mm to that, which is about the thickness of a sheet of paper. So Z_original - Z_error + 0.1 = Z_correct
8. Disconnect from Pronterface, open Arduino, open Marlin, set the value
Z_MAX_POS to Z_correct in configuration.h and upload.
9. Once upload is finished heat up bed and nozzle as they will have cooled, home the

M90LC Manual | 62 of 70 | V0.4-20131016

printer and type M114 - this should now be the correct value for z_correct.

10. Centre the nozzle in X and Y, type G1 Z5 or move the nozzle down to just above the bed, then do the paper trick again and the paper should bind when M114 reports Z= ~0.1mm.

Extruder E-steps calibration.

1. Move the nozzle so it is clear of the bed (half way up the Z axis) and heat to 200C for PLA or 250 for ABS
2. “Disable Motors” then insert filament by hand, turning the large gear to feed it through until some is extruding.
3. Using a set of callipers or an accurate ruler measure up 30mm from where the filament enters the top of the extruder block. Mark with a felt tip pen.
4. Using Pronterface extrude 20mm then switch to 1mm extrudes, counting the total distance commanded until the felt tip mark lines up with the top of the extruder block. Measure again and repeat, ensuring that the same result occurs. (If they are different try once more, if still getting varying amounts then there is a problem with the filament feed. Check the spring tightness). In this example, assume distance commanded to feed a measured 30 mm is actually 32 mm, substitute you own measurements.
5. Calculate the new E steps value in the following way:

(distance commanded/distance measured) * current E_Steps = new E_steps

The original E_steps set in firmware was 520 so the first time this is done current E_Steps is 520.

e.g. (32/30) * 520 = 554.6 ~ 555 mm

Enter the new E_steps in Pronterface using “M92 E555”. At this point extrude 10mm to get round a bug in the firmware that messes with the first extruded amount following the M92 command.

6. Repeat steps 2. to 6. until there is <1mm difference between what is commanded and measured.
7. Use M500 to store the settings then M503 to check the current settings.
8. Repeat steps 2 to 6 with an extrusion length of 60mm, remembering to change the distance measured in the formula to 60. Once again stop once the difference is <1mm.

Repeat step 8 with 100mm, at the end of this the error is <1%

Calibration objects.

1. Treat the bed according to the type of filament (eg hairspray for PLA, ABS juice for ABS).
2. Unzip the appropriate version of Slic3r (32 or 64-bit), run it and Import the M90LC_default_PLA_config.ini configuration file.
3. Measure your filament diameter with the callipers: ensure the filament is measured directly across, straightened out of the natural curve, and make multiple measurements and take the average. Our standard filament 2.85-2.9 mm.
4. Add the 30mm hollow box and export G-code then print.

M90LC Manual | 63 of 70 | V0.4-20131016
5. You have successfully printed your first object, a simple single walled cube. The advanced calibration section in the User Manual will contain tips for further calibration however at this point the printer is calibrated. The final task is to fit the fan and the acrylic enclosure if that option has been purchased.

Fitting the fan

1. Slide the fan assembly's bracket onto the M3 screws on the front of the carriage and tighten them. The fan should sit level. If it droops downwards it may foul the clips holding the glass. In which case add a shim between the bracket and the carriage above the screws to make it level.
2. Plug the fan into the 3 pin connector on the distribution PCB. The red and black wires should line up with the F+ and F- labels.

To test type M106 in Pronterface to turn the fan on and M107 to turn it off. The Slic3r profiles can be adjusted to control when the fan come on during printing.

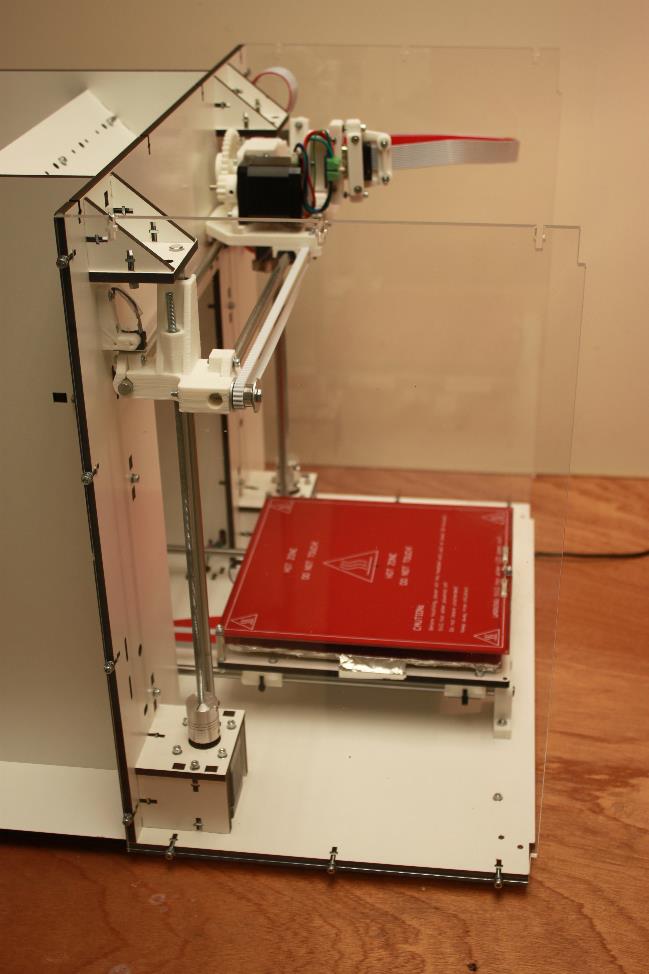
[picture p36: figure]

M90LC Manual | 64 of 70 | V0.4-20131016

### 20. Acrylic Enclosure Assembly

The acrylic enclosure is fitted using the same fastening method at the frame. In the same way as the frame, the laser cutting process means that the holes are slightly wider on one side so if a square nut does not fit easily from one side, try the other side. Take care to align the acrylic panels with the frame as the screws are tightened.

When moving the printer about during this process take care to control the X and Y carriage so that they don’t crash from end to end.

Side panels

These are fitted first with the slots for the door hinges to the front and the “t” shaped cutouts to the top.

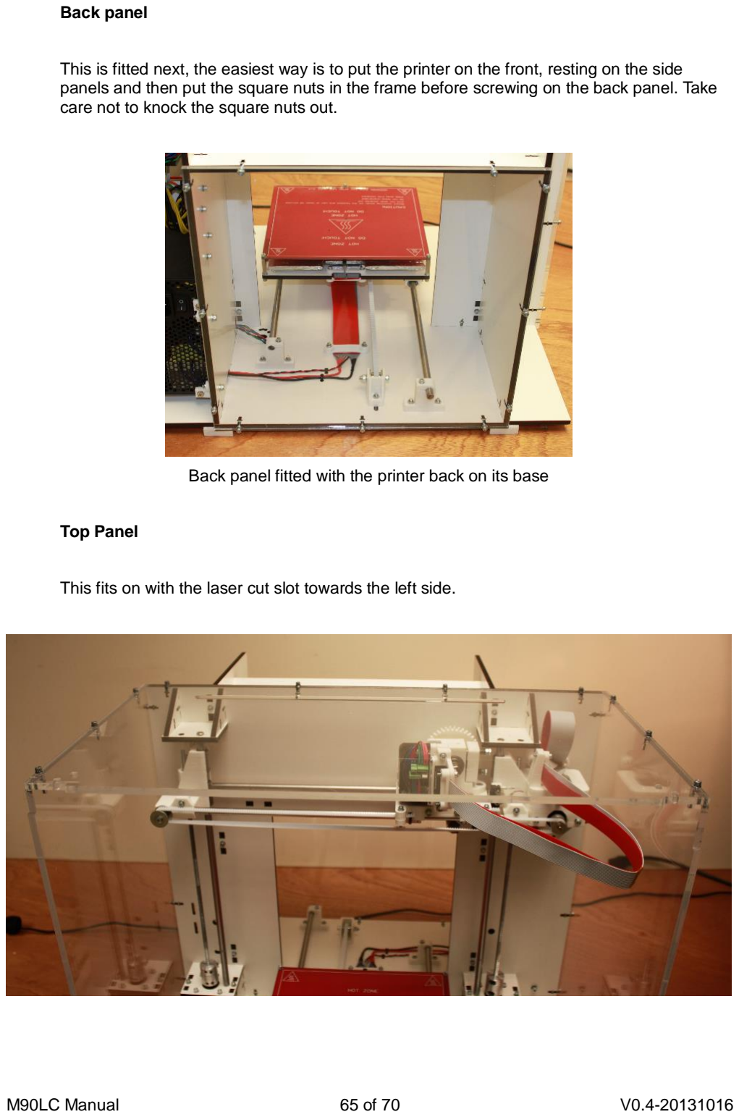
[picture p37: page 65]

M90LC Manual | 65 of 70 | V0.4-20131016

Back panel

This is fitted next, the easiest way is to put the printer on the front, resting on the side panels and then put the square nuts in the frame before screwing on the back panel. Take care not to knock the square nuts out.

Back panel fitted with the printer back on its base

Top Panel

This fits on with the laser cut slot towards the left side.

M90LC Manual | 66 of 70 | V0.4-20131016

Doors

The door hinges are adjustable to allow for exact alignment up and down and the frame and the hinges are slotted to allow for left and right and forward and backwards adjustment.

Apply the back rubber pads to a top and bottom corner of each door. These pads are to prevent damage to the acrylic and increase the hinge grip.

The hinges are right and left handed, identify which way round they go then attached them to the doors using the black plastic screw. Tighten the screw enough that they do not fall all but do not over tighten, these will be adjusted further in a later step.

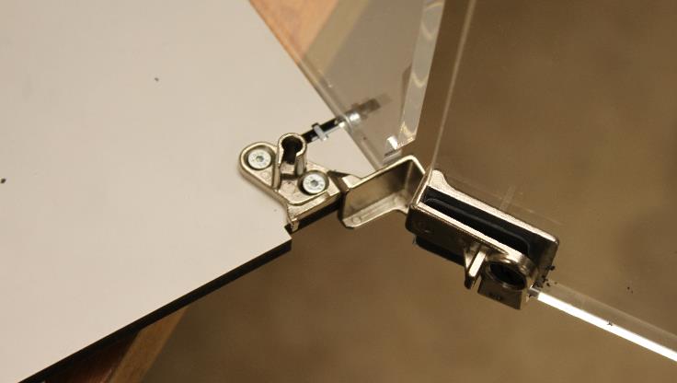
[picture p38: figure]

M90LC Manual | 67 of 70 | V0.4-20131016

Fit the hinges with the countersunk screws in the hinge groves and the washers and nyloc nuts on the other side of the top acrylic panel at the frame base.

Once fitted, close the doors, it is likely they will not line up perfectly first time. Use the adjustability in the hinges to set first one door then the other square with the top acrylic panel and then adjust left and right until they close with no gap.

M90LC Manual | 68 of 70 | V0.4-20131016

### 21. Operating Instructions

These operating instructions are enough to get started with using the printer. More detailed instructions will be contained in the upcoming user manual.

Heated Bed

The purpose of the heated bed is twofold: to reduce warping and to make the first layer stick. In general molten plastics don't stick well to cold smooth surfaces but they will stick to some hot surfaces.

As each layer is laid down it cools and shrinks a little due to thermal contraction. The second layer welds on to the first layer and then tries to contract, putting stress on it. The next layer does the same and eventually the cumulative stress becomes enough to overcome the adhesion of the first layer to the bed and the corners start to lift and curl up. By keeping the object warm the amount of contraction is reduced until the bed is switched off at the end and then all the layers cool to room temperature together.

The ideal temperature for the surface of the bed is just below the glass transition temperature of the plastic (Tg). This is the temperature at which the plastic transitions from a rubbery state to a rigid or glass like state. As the plastic cools from the molten state all the way down to Tg it isn't solid enough to stress the layer below. Stopping it cooling just below Tg means it doesn't contract much at all past the point where it is solid enough to stress the layer below and it is rigid enough to support the layer above.

The temperature of the bed is measured underneath, so the temperature at the surface of the glass is around 15˚C lower. PLA has a glass transition around 55˚C, so 70˚C is a good temperature to set the bed to. It can be set to a higher temperature for the first layer to increase adhesion, but after that it must be below Tg.

At the end of the build PLA objects will come loose when the temperature drops below about 35˚C due to the different contraction rate of the plastic and the glass.

ABS is more difficult because it has a higher glass transition and higher thermal expansion coefficient. In addition it doesn't stick well to bare glass. A bed set temperature of 120˚C-130˚C is needed and the bed struggles to reach that temperature without insulation under it. Covering the top surface with a sheet of corrugated cardboard makes it warm up much faster.

To make ABS stick to the glass it will need some form of coating. A thin layer of a dilute solution and ABS in acetone works. PET or Kapton tape gives more adhesion but the disadvantage is the objects don't come loose when the bed cools and need to be prised off. Changing filament

Do not to let the extruder run out of filament. If it does it will lose grip as soon as it gets past the hobbed bolt, making it difficult to remove as you cannot simply rewind it. You would have to remove the idler screws and grab the end with snipe nose pliers and pull it out while hot.

Removal

To change to a new reel of filament heat the extruder to normal operating temperature then rewind 100mm at ~120mm/min. When the bit that has been molten gets to the hobbed bolt there will come a point where it is too thin or soft to be gripped. At this point pull it with enough hand tension to stop it from slipping and keep up the tension until it is all the way out. Do not stop rewinding it when it is part way out. This can cause soft filament to

M90LC Manual | 69 of 70 | V0.4-20131016

expand into the entrance of the J-Head (which is bigger than the filament path) and jam there as it freezes.

If you are switching between a strong colour and a weaker one it can take a long time to flush through all the pigment. To minimise this you can remove PLA at 80˚C (which is above its glass transition temperature but below its melting point). As it is therefore not a liquid but a rubbery solid, it will pull out in one piece leaving very little behind. It does stretch a lot though, so you need to rewind about 150mm to get it all out. The same trick can by done with ABS at 150˚C.

Do not leave the extruder hot without filament as the plastic residue inside will oxidise and become baked on to the inside of the melt chamber. Switch off the heater if you are not going to reload it immediately.

Insertion

To insert the new filament press the “Motors off” button, push the filament into the extruder while turning the big gear by hand. It is important to apply enough force to get the filament to open the idler without it slipping against the hobbed bolt. If the bolt slips against the plastic its teeth can get clogged.

Different types of filament

Different filaments require different temperatures. Not only does the type of plastic, but even the colour, makes a big difference. The village PLA from Faberdashery that is supplied with the kit is happy at 200˚C colours can vary. The pigments change how viscosity varies with temperature.

Failure to use an appropriate temperature may cause the extruder to become blocked. When trying a new filament for the first time turn the extruder motor off and try feeding it by hand turning the big gear. If the temperature is too low it will be very stiff to turn. If it is too high it will drip out the nozzle like syrup rather than forming a solid filament. Other signs of it being too hot are discolouration or smoke. Don't select a temperature higher than 250˚C as it will damage the hot end.

Cleaning the hobbed bolt

In normal use the hobbed bolt does not need cleaning. If the filament starts slipping for any reason, such as not enough spring tension, or the nozzle is blocked then its teeth can become clogged with plastic. It will then not give consistent grip until it is cleaned.

- Remove the filament by the method described above.
- Lower the Z axis so the extruder is below the gantry.
- Undo the M8 nuts and remove the big gear and the hobbed bolt.
- Clean the bolt with a wire brush.
- Reassemble and reload the filament.

PID Autotune

Marlin has built in PID control for the Extruder and Bed that allows for smoother temperature control. There is a built in function to get the correct values for PID for both the extruder and the heated bed.

For the extruder type
M303 E0 C6 S210
In pronterface, this will run 6 cycles of PID autotune up to 210C. If you are mainly printing in ABS or at a different temperature the replace 210 with your normal extrusion temperature.

For the bed type
M303 E-1 C6 S70

M90LC Manual | 70 of 70 | V0.4-20131016

Or whatever your standard bed temperature is.

One you have the values of Kp, Ki and Kd for the extruder and bed they can be entered into Marlin, find the lines below and enter your autotuned values:

//for the extruder
#define | DEFAULT_Kp 32.35

#define | DEFAULT_Ki 2.58

#define | DEFAULT_Kd 101.49

//for the bed
#define | DEFAULT_bedKp 120.69

#define | DEFAULT_bedKi 6.86

#define | DEFAULT_bedKd 531.14

In addition the Extruder ones should be saved to EEPROM

M301 P32.35 I2.58 D101.49

Replacing the numbers with your autotuned ones. Dont forget to use M500 to store the settings once changed.

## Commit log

2013-10-02 Mendel90 LC first commit
    The changes to the default Mendel90 SCAD files for the Mendel90
    Lasercut.
    details here:
    http://blog.think3dprint3d.com/2013/09/mendel90-laser-cut-ready-to-print.html
    [alu_channel_cap.scad, bar-clamp.scad, bars.scad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]
2013-10-02 RRP Extruder
    The RepRapPro Extruder which is used as a model to show how the 5
    extruder mount could be used in the future - direct copy from here:
    https://github.com/reprappro/Extruder-drive.
    [config.scad, extruder-drive.scad, extruder-drive.stl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]
2013-10-02 Plastic Part STLs for the Mendel90 Lasercut
    Main changes are:
    X-Motor end, the endstop position is raised in order to clear the
    pushfit cable connectors and the hole they fit through is enlarged.
    Y carriage, raised slightly so if using 3 point bed leveling with a
    central hex pillar the screw clears the motor housings
    Bearing Holders, sligtly less "grippy" as the zip ties hold them in
    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
    [ATX_PSU_brackets.stl, alu_channel_cap.stl, d-motor_bracket.stl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]
2013-10-02 Stubborn files that would not sync first time
    [ATX_PSU_brackets.scad, bed.scad, bom.scad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]
2013-10-03 comment error fixed
    [electronics.scad]
2013-10-03 New X-Idler bracket from Nophead's update
    Uploaded now mainly as a demonstration for the Slic3r issue (#1472) with
    enclosed voids.
    [x-idler-bracketv1.1.stl]
2013-10-07 Integrating new X Idler and Motor brackets
    Update based on Nophead's new design:
    http://hydraraptor.blogspot.co.uk/2013/10/mendel90-design-improvements.html
    also updated the blog post on assembly
    http://blog.think3dprint3d.com/2013/10/mendel90-lasercut-overview.html
    [ATX_PSU_brackets.scad, ball-bearings.scad, bar-clamp.scad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]
2013-10-15 Minor changes to top limit switch length
    and the correct x_end_clamp for the idler and motor end when re-sized
    form M5 threaded rods.
    [x_end_clamp.stl, z-top-limit-switch.stl]
2013-10-21 Re-organise lasercut directory structure
    [ATX_PSU_brackets.stl, alu_channel_cap.stl, d-motor_bracket.stl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]
2013-10-21 frame dxf files added
    [T3P3_LC_M90_Acrylic_v1.0_back.dxf, T3P3_LC_M90_Acrylic_v1.0_door.dxf, T3P3_LC_M90_Acrylic_v1.0_side.dxf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]
2013-10-21 Assembly instructions
2013-10-31 Dual extruder support
    New fork for experimental dual extruder support.
    more details on this blog post:
    http://blog.think3dprint3d.com/2013/10/dual-extruders-on-lasercut-mendel90.html
    [D_bracket_RRPEv0.3.stl, simple40mmfanbracket_RRPEv0.3.stl, x-carriage.scad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]
2014-01-09 X Carriage update for Kraken
    See
    http://blog.think3dprint3d.com/2014/01/4-extruder-printing-duet-kraken.html
    [D_bracket_k_v0.2.stl, x-carriage-kv2.scad, x-carriage_K_v0.2.stl]
2014-10-28 e3d V6 bowden hotend mount, x-carriage and fan duct
    [D_bracket_g_v0.2.stl, x-carriage - gv0.3.stl, x-carriage - gv1.scad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]
2014-11-16 d_bracket_g_v0.2 inverted on Z
    So it sits correctly on the build plate
    [D_bracket_g_v0.2.stl]
2014-12-20 Fixed D bracket model
    [D_bracket_g_v0.2.stl]
